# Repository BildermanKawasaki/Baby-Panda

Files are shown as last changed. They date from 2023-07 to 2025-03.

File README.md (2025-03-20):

# Baby-Panda 🐼
#### CoreXY Continuous Printing

Baby Panda is a CoreXY printer with conveyor build plate to enable affordable high quality continuous printing. The motion system is based on the [Voron 2.4](https://vorondesign.com/voron2.4), with z motor mounts and skirts modified to accommodate the conveyor.  The design is intended to repurpose as many parts as possible from a pair of Ender 3s.

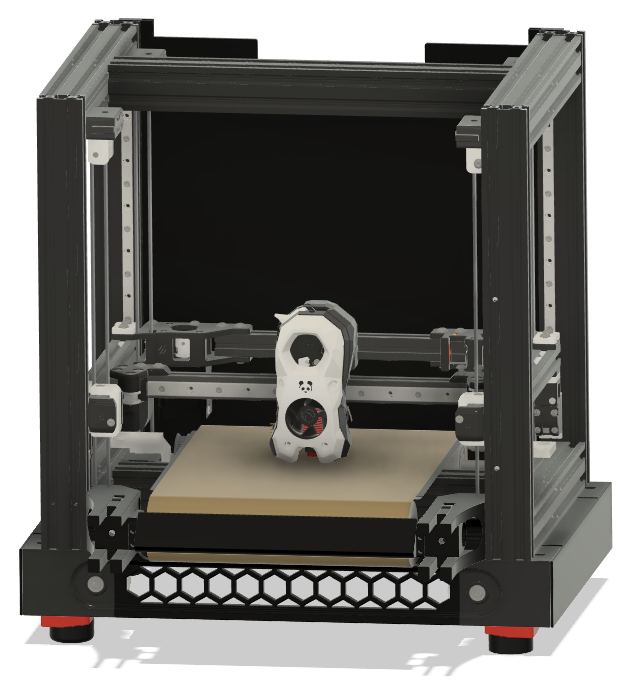
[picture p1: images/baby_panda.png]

If you like this project, please consider <a href="https://www.ko-fi.com/robxberty">tipping</a>!
## Building Baby Panda
There are currently no build instructions specific to Baby Panda, so but the [Voron 2.4r2 assembly manual](https://github.com/VoronDesign/Voron-2/raw/Voron2.4/Manual/Assembly_Manual_2.4r2.pdf) can be used for the most part, along with the following reasources for the Baby Panda-specific parts:
* [BOM](https://github.com/robwaldhauser/Baby-Panda/blob/main/BOM%20Spreadsheet.ods) - Baby Panda bill of materials (.ods format)
* [STLs](https://github.com/robwaldhauser/Baby-Panda/tree/main/STLs) - model files for each part
* [CAD](https://github.com/robwaldhauser/Baby-Panda/tree/main/CAD) - An archive containing a .step file with a fully assembled Baby Panda

If you have any questions, or want to see pictures and videos of builds, check out the #🐼baby-panda channel in the [Build Biome Discord server](https://discord.gg/SpCVg9wG). 

## Ender 3 Parts Reuse
As mentioned above, one of the goals of this project is to repurpose parts from Ender 3s that are sitting around gathering dust. Some of the parts that can be reused include:
* All base 4040 extrusions (Pro/V2)
* Y 4040 extrusion (Pro\*)
* 4020 extrusions (Pro/V2)
* Power supply
* Mainboards\**
* Motors
* Bed carriage
* Heated bed
* Some wiring

\*V2 Y 4040 extrusion could be reused with spacers
\*\*A total of 8 motors drivers are needed, but if you have 2 mainboards they can both be used

## The Belt Assembly
This assembly is the heart of the project. It adds one additional stepper motor to the BOM. There is nothing official released yet, but several people in the Discord are working on macros to make it work. The purpose of the belt is to eject printed parts automatically after printing so that another job can run immediately and without intervention. It is not intended to move during a print as X-Y movement is handled by the coreXY motion system.
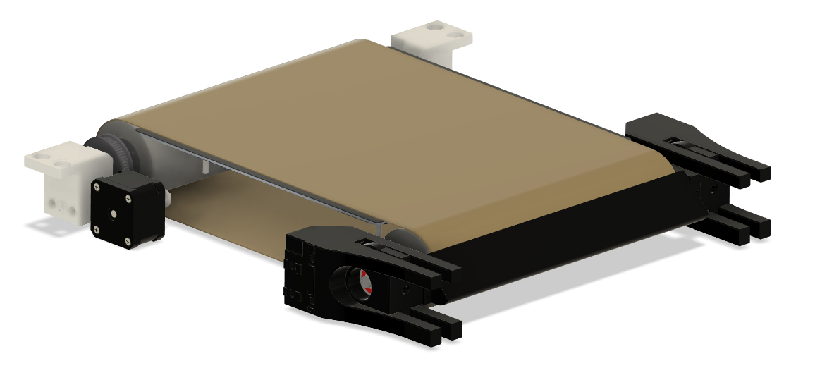
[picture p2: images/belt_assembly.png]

<p><em>Belt assembly</em></p>

## The Frame
The standard Baby Panda frame can be built entirely from extrusions salvaged from 2 Ender 3s. Ender 3 pro is ideal. 3V2 can work, but the Y extrusion is slightly shorter. This can be worked around using spacers or by buying a longer extrusion.

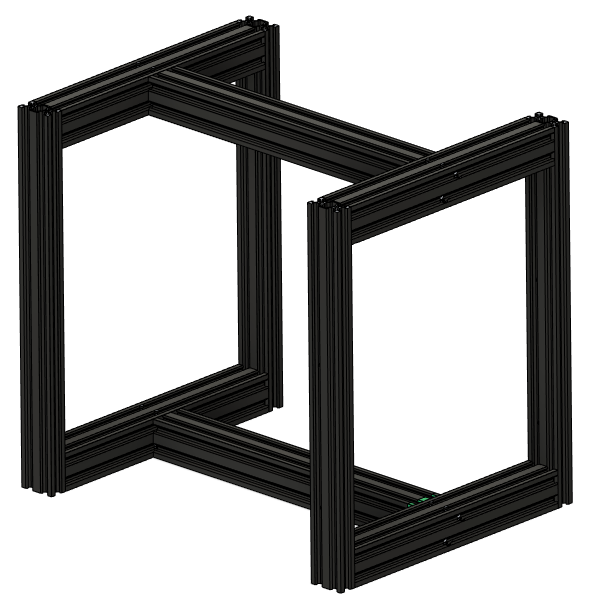
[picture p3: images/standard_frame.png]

<p><em>Standard frame</em></p>

<p>In the standard configuration, the 3 4040 extrusions from the base of one Ender form the base of the Baby Panda frame, and the base extrusions of the other Ender  form the top. The uprights from each ender, which will need to be drilled out for blind joints using the <a href="https://github.com/robwaldhauser/Baby-Panda/blob/main/STLs/Drilling%20Jig.stl">jig</a> available in the CAD section, connect the top of the frame to the bottom in each corner. In case you're not familiar with drilling/tapping new blind joints, <a href="https://www.youtube.com/watch?v=2dvbn0rWA60&ab_channel=CanuckCreator">this video</a> is really helpful. Optionally, 2 additional 2020 extrusions can be installed for extra rigidity and to help enclose the printer.</p>

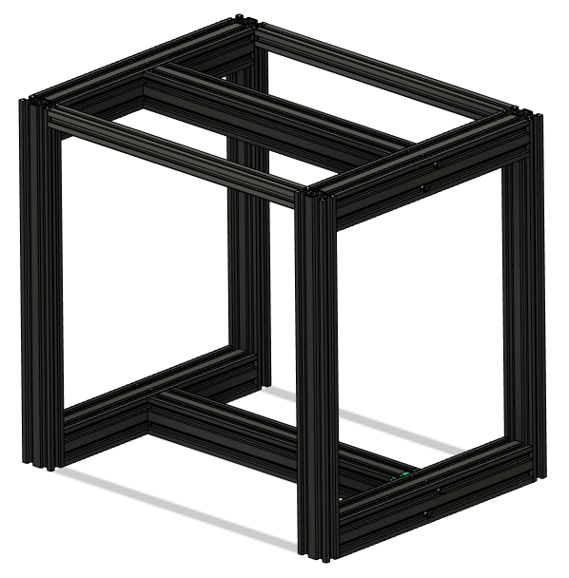
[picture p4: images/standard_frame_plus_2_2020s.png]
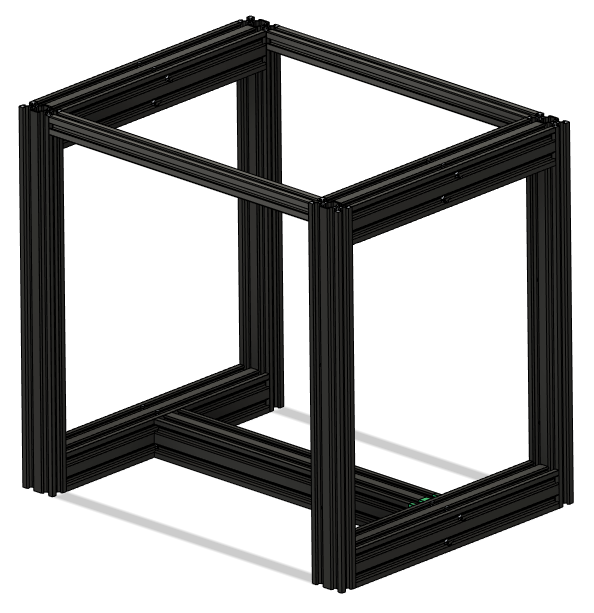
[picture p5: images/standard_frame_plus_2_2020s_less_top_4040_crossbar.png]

<p><em>A couple options for placement of additional 2020 extrusions</em></p>

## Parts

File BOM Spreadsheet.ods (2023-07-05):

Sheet: BOM
Required | Category | Item | URL | Qty | Subtotal | Total
Y | Motion | Linear Rail for X Axis - MGN12H, 280mm | https://www.aliexpress.com/item/3256804722090559.html | 1 | $11.93 | $11.93
Y | Motion | Linear Rail for Y Axis - MGN9H, 220mm | https://www.aliexpress.com/item/3256804722090559.html | 2 | $9.18 | $18.36
Y | Motion | Linear Rail for Z Axis - MGN9H, 300mm | https://www.aliexpress.com/item/3256804722090559.html | 4 | $10.45 | $41.80
Y | Motion | Voron Motion Kit | https://www.aliexpress.com/item/3256803752663278.html | 1 | $53.39 | $53.39
 | Hotend Assembly | Stealthburner Parts | https://www.aliexpress.us/item/3256804449233315.html | 1 | $41.85 | $41.85
 | Hotend Assembly | Tap | https://www.aliexpress.com/item/3256805352633425.html | 1 | $20.80 | $20.80
 | Motherboard | M8P+CB1+8TMC2209 | https://biqu.equipment/products/manta-m4p-m8p?variant=39847239155810 | 1 | $98.68 | $98.68
 | Hotend Assembly | SB2209 CAN for Stealthburner | https://biqu.equipment/products/bigtreetech-ebb-sb2209-can-v1-0?variant=40214282731618 | 1 | $25.68 | $25.68

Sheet: Sheet1
 | Part | Path | Github Repo | Qty | Function Part
Z Axis | NEW_z_drive_main_a_x2
 | NEW_z_drive_main_b_x2
 | z_drive_retainer_a_x2.stl | STLs/Z_Drive | VoronDesign/Voron-2 | 2 | TRUE
 | z_drive_retainer_b_x2.stl | STLs/Z_Drive | VoronDesign/Voron-2 | 2 | TRUE
 | [a]_belt_tensioner_a_x2.stl | STLs/Z_Drive | VoronDesign/Voron-2 | 2 | TRUE
 | [a]_belt_tensioner_b_x2.stl | STLs/Z_Drive | VoronDesign/Voron-2 | 2 | TRUE
 | [a]_z_drive_baseplate_a_x2.stl | STLs/Z_Drive | VoronDesign/Voron-2 | 2 | TRUE
 | [a]_z_drive_baseplate_b_x2.stl | STLs/Z_Drive | VoronDesign/Voron-2 | 2 | TRUE
 | z_tensioner_bracket_a_x2.stl | STLs/Z_Idlers | VoronDesign/Voron-2 | 2 | TRUE
 | z_tensioner_bracket_b_x2.stl | STLs/Z_Idlers | VoronDesign/Voron-2 | 2 | TRUE
 | [a]_z_tensioner9mm.stl | STLs/Z_Idlers | VoronDesign/Voron-2 | 4 | TRUE

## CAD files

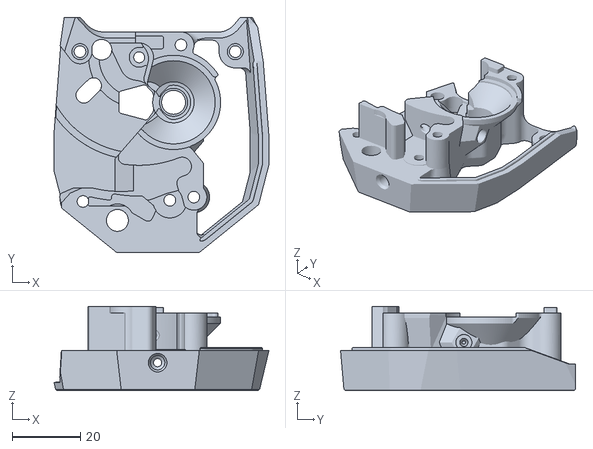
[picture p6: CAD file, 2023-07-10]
STLs/Voron-Stealthburner-main/Clockwork2/main_body.stl
62.8 x 68.7 x 24.7

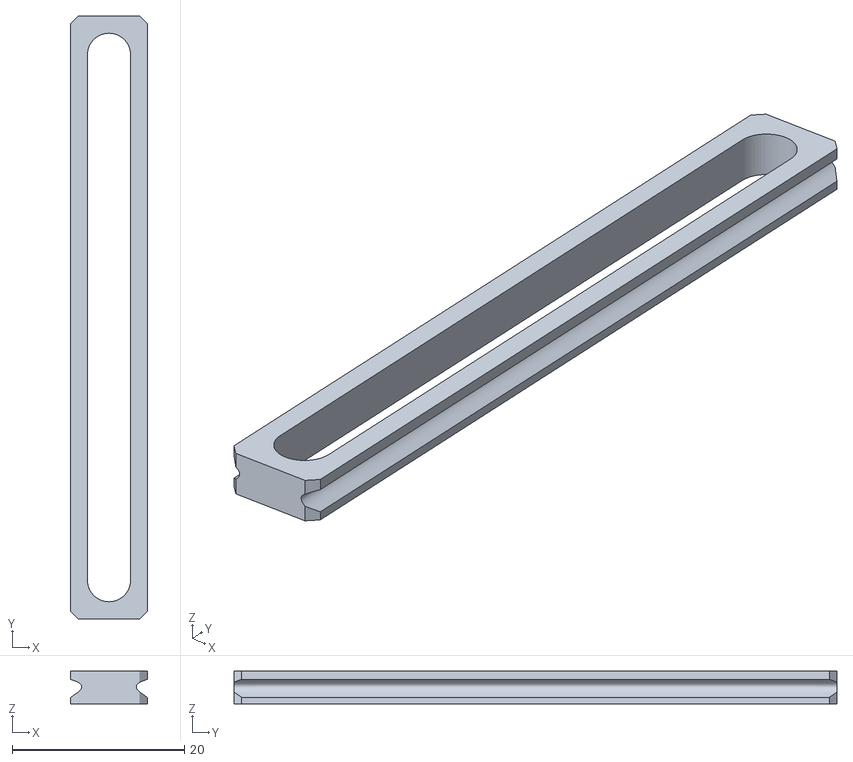
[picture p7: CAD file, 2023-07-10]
STLs/Voron-Tap-main/MGN9_Assembly_Tool.stl
8.90 x 70.0 x 3.80

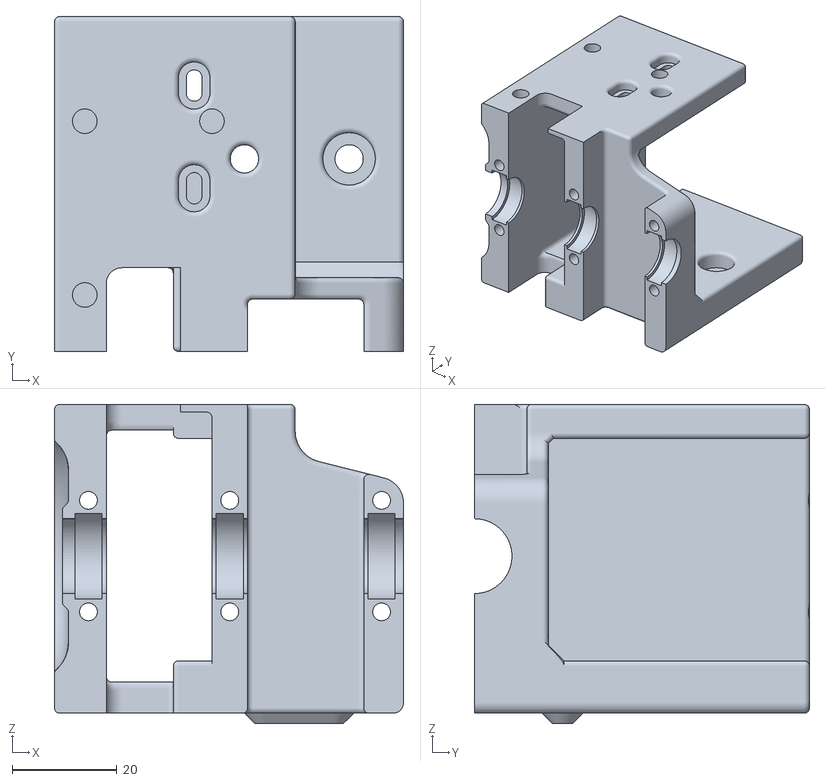
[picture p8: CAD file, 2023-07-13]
STLs/Z_Drive/BP_z_drive_main_b_x2_wSupport.stl
66.7 x 64.0 x 61.0

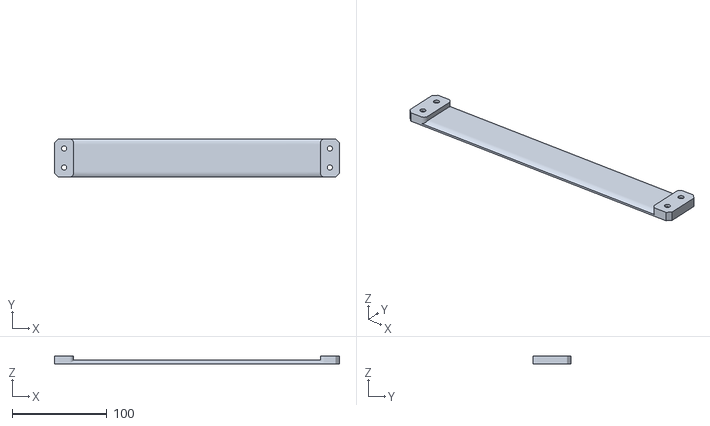
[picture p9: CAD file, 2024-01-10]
STLs/Baby Panda Parts/Belt Shield.stl
300.1 x 40.0 x 8.74

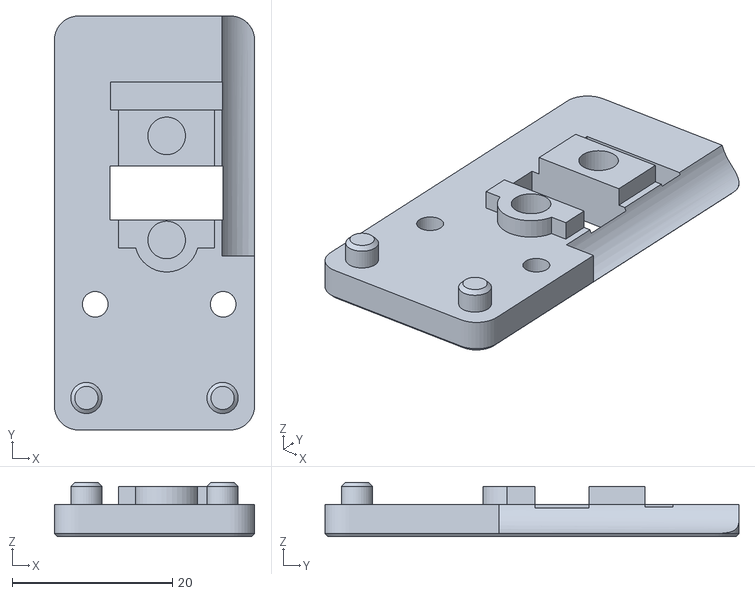
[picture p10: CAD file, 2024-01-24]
STLs/CAN/Y_endstop_[a]_B.STL
25.0 x 51.7 x 6.80

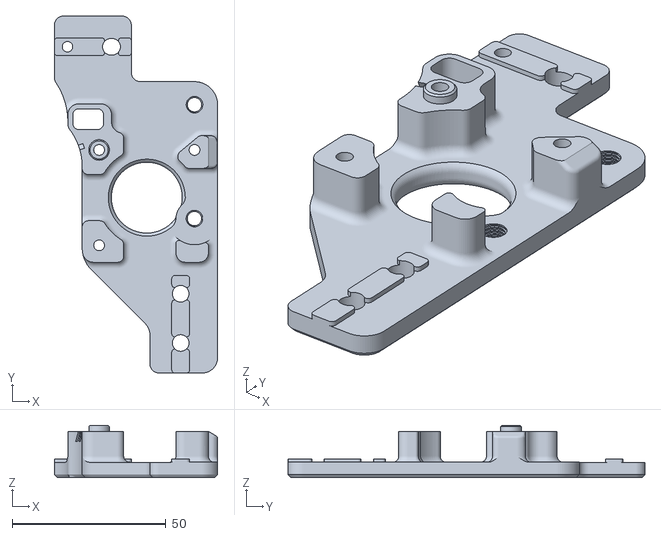
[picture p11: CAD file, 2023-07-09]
STLs/Gantry/AB_Drive_Units/b_drive_frame_lower.stl
53.0 x 116.0 x 17.0

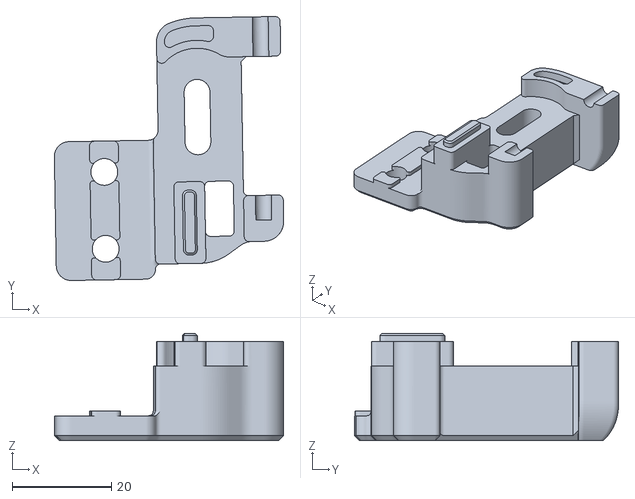
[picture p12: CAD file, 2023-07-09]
STLs/Gantry/Front_Idlers/front_idler_left_upper.stl
46.2 x 53.2 x 21.6

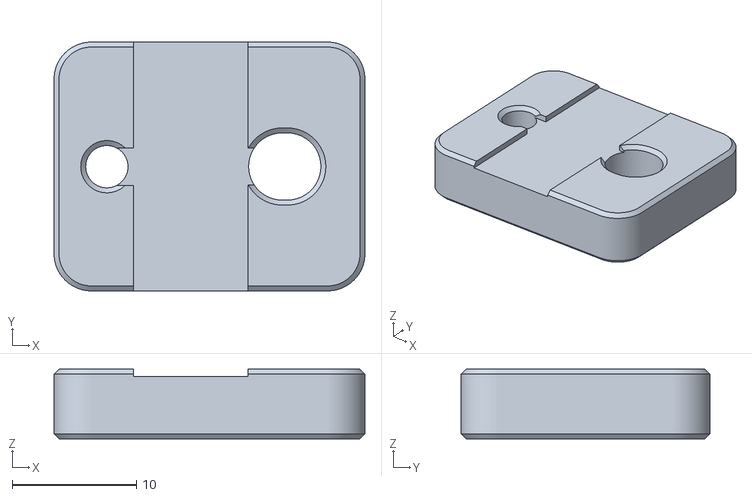
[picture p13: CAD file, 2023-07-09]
STLs/Gantry/ignore - [a]_z_belt_clip_lower_x4.stl
25.0 x 20.0 x 5.60

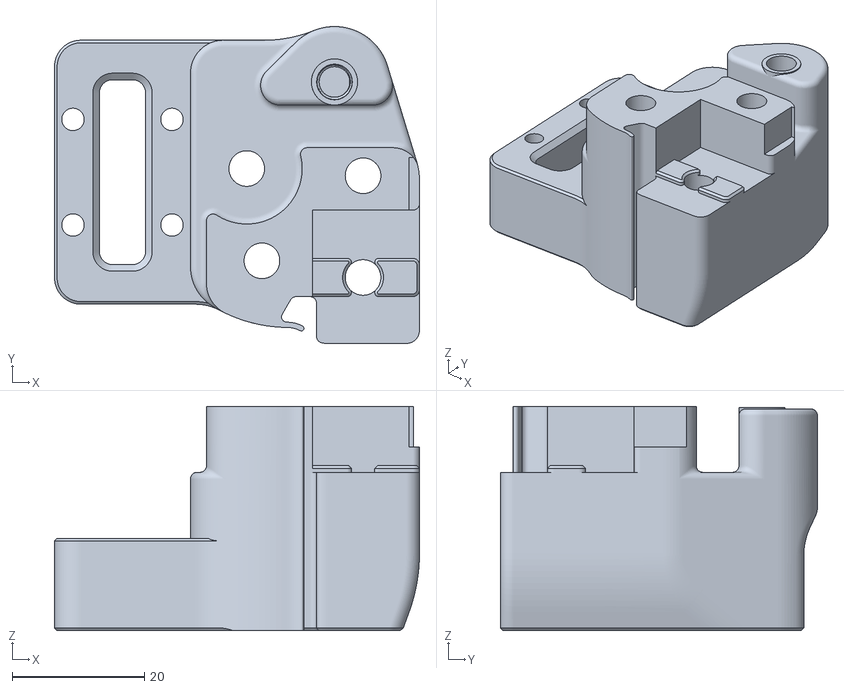
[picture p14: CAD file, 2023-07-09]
STLs/Gantry/X_Axis/XY_Joints/xy_joint_right_lower_MGN12.stl
55.3 x 48.0 x 34.0

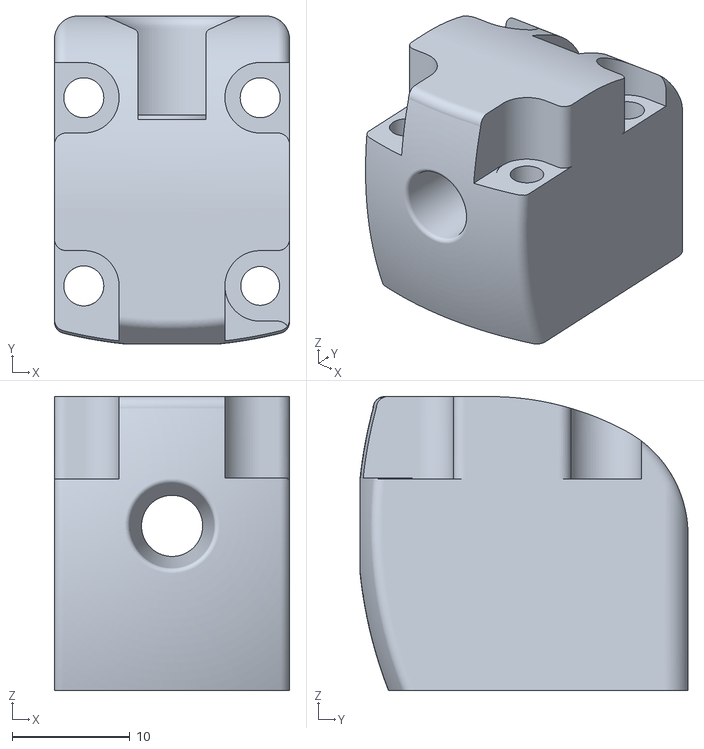
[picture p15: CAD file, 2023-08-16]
STLs/Gantry/Z_Joints/BP_z_joint_lower_x4.stl
20.0 x 27.9 x 25.0

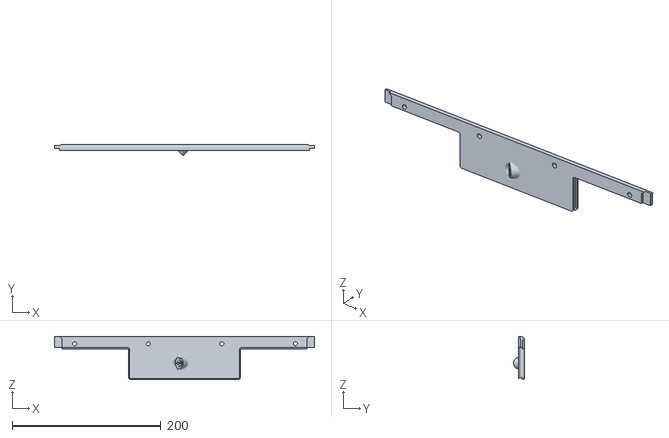
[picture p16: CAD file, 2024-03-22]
STLs/Panels/Back Panels/PTFE Passthrough.stl
350.0 x 14.6 x 58.2

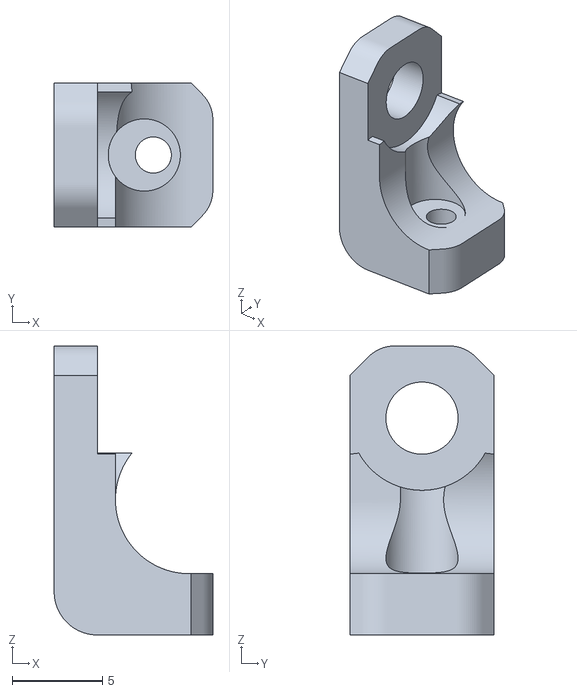
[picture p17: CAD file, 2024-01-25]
STLs/Panels/Bottom Panels/PSU Clip.stl
8.80 x 8.00 x 16.0

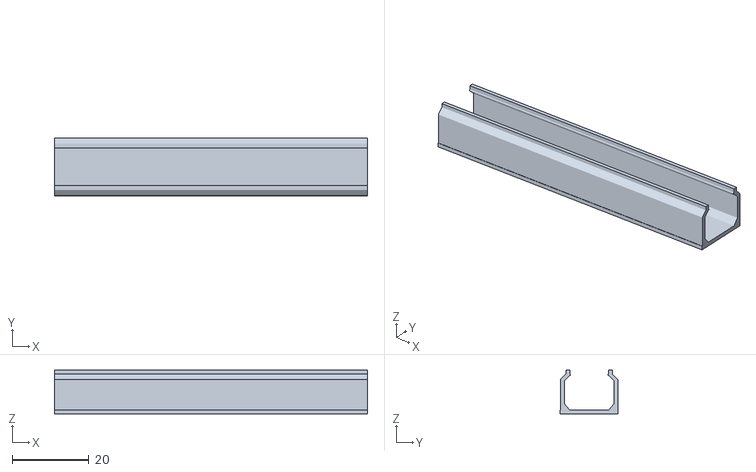
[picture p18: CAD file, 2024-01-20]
STLs/Panels/Cable Track.stl
81.6 x 15.0 x 11.5

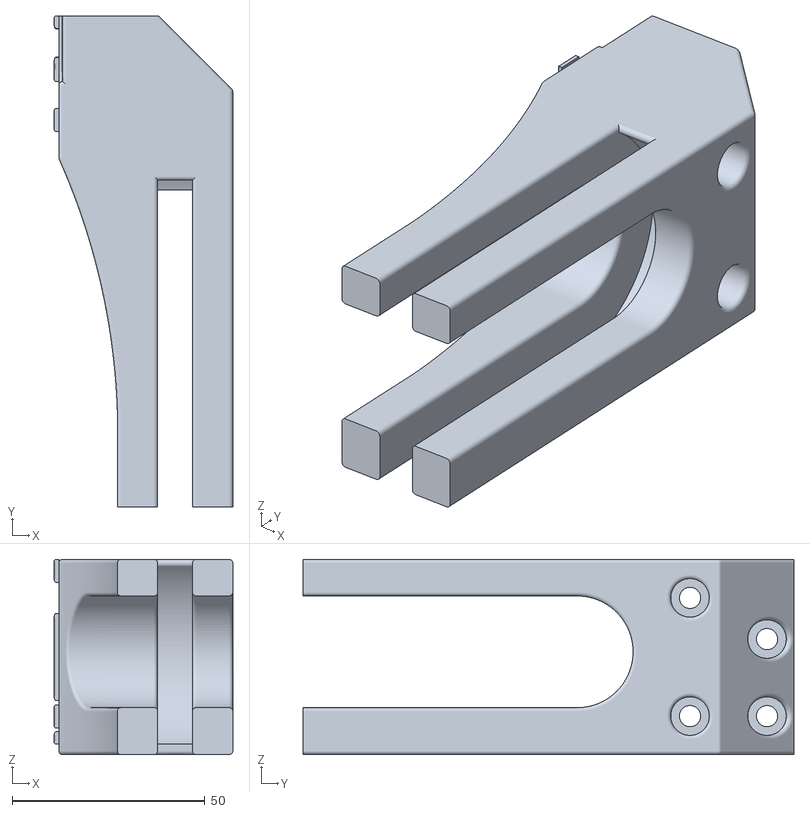
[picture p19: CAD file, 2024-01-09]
STLs/Roller Parts/Left Roller Arm_x2_but_mirrored.stl
46.4 x 127.5 x 50.7

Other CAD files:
STLs/Z_Drive/BP_z_drive_main_a_x2_wSupport.stl
STLs/Skirt/Front Skirt.stl
STLs/sturdy_handles.stl
STLs/Voron-Stealthburner-main/Clockwork2/cable_door.stl
STLs/3mm riser (opt).stl
STLs/59mm Roller.stl
STLs/BP_Roller_Blade.stl
STLs/Baby Panda Spool Holder.stl
STLs/CAN/Drag Chain Lower Mount.stl
STLs/CAN/Extrusion Cover.stl
STLs/CAN/TPU Umbilical Holder.stl
STLs/CAN/Y_endstop_A.STL
STLs/Drilling Jig.stl
STLs/Gantry/AB_Drive_Units/[a]_z_chain_retainer_bracket_x2.stl
STLs/Gantry/AB_Drive_Units/a_drive_frame_lower.stl
STLs/Gantry/AB_Drive_Units/a_drive_frame_upper.stl
STLs/Gantry/AB_Drive_Units/b_drive_frame_upper.stl
STLs/Gantry/Front_Idlers/[a]_tensioner_left.stl
STLs/Gantry/Front_Idlers/[a]_tensioner_right.stl
STLs/Gantry/Front_Idlers/front_idler_left_lower.stl
STLs/Gantry/Front_Idlers/front_idler_right_lower.stl
STLs/Gantry/Front_Idlers/front_idler_right_upper.stl
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

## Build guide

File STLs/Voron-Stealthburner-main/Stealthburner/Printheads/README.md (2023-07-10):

# Printheads for Stealthburner.

Choose files containing ***front*** based on your hotend and ***rear_cw1*** / ***rear_cw2*** based on whether you're using the original Clockwork (CW1) or the new Clockwork2 (CW2) extruder.

## Printhead Compatibility:

| Hotend | Compatible Parts | Notes |
|---|---|---|
| Phaetus/Trianglelab Dragon | (P-DRG) | Remove the screws attaching the groove-mount adaptor to access the hard mounting points. |
| Phaetus BMO | (P-BMO) | Unscrew the groove-mount adaptor to access the hard mounting points. |
| Phaetus BMS (6 fins) | (P-BMS6) | Phaetus has two versions of the BMS; Count the number of fins on your hotend to determine your version. |
| Phaetus BMS (7 fins) | (P-BMS7) | Phaetus has two versions of the BMS; Count the number of fins on your hotend to determine your version. |
| Phaetus Rapido | (P-RPD) | Only the standard Rapido is supported (No UHF support). See the additional note about [heatsink orientations](phaetus_rapido/README.md). |
| E3D Revo Micro | (E-RM) | If your mount nut has a ridge on it, put that to the top. |
| E3D Revo Six | (E-V/R6) |  |
| E3D V6 | (E-V/R6) |  |
| E3D Revo Voron | (E-RV) |  |

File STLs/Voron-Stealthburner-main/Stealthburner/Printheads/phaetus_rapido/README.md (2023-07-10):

## Phaetus Rapido High Flow mount

### BOM

- One front printed part
- One rear printed part
- Heatset inserts
- Four M2.5x8 socket screws, which should be provided in your Rapido kit
- Two M3x12 socket screws
- PTFE tube

### Instructions

- Add two heatset inserts on the front printed part. Add an additional two if you plan to use the ADXL PCB mount.
- Remove the adapter and bowden collet from the Rapido's heatsink by unscrewing the two M2.5x5 screws:
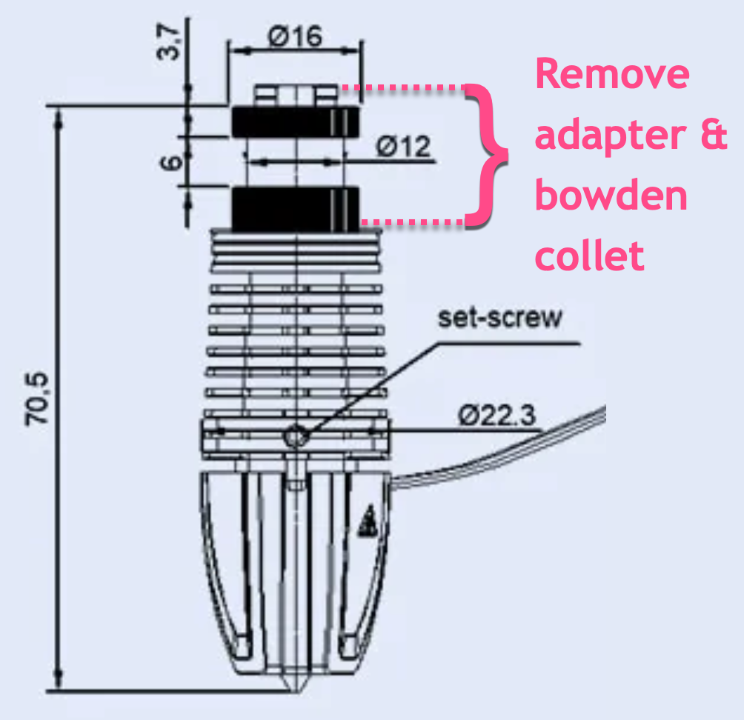
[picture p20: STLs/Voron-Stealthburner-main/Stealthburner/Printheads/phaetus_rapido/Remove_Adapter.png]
Remove adapter
  
- Place the hotend in the front printed part and secure it by screwing two M2.5x8 screws into the heatsink.
- Secure the front and rear printed parts together with two M3x12 screws.
- Secure the hotend with the rear part by screwing two M2.5x8 screws into the heatsink.
- Insert the PFTE tube at the top of the mount.

### A note about Rapido orientations

Depending on where the Rapido is sourced, it may come in one of two unsupported heatsink orientations.

To change the orientation of heatsink, first loosen the grub screw on the side and then remove the 3 screws around the heater core. The heatsink can then be rotated +/- 120° into the correct orientation. Be careful not to over-tighten the screws when reassembling as this could cause the heatbreak to bend.

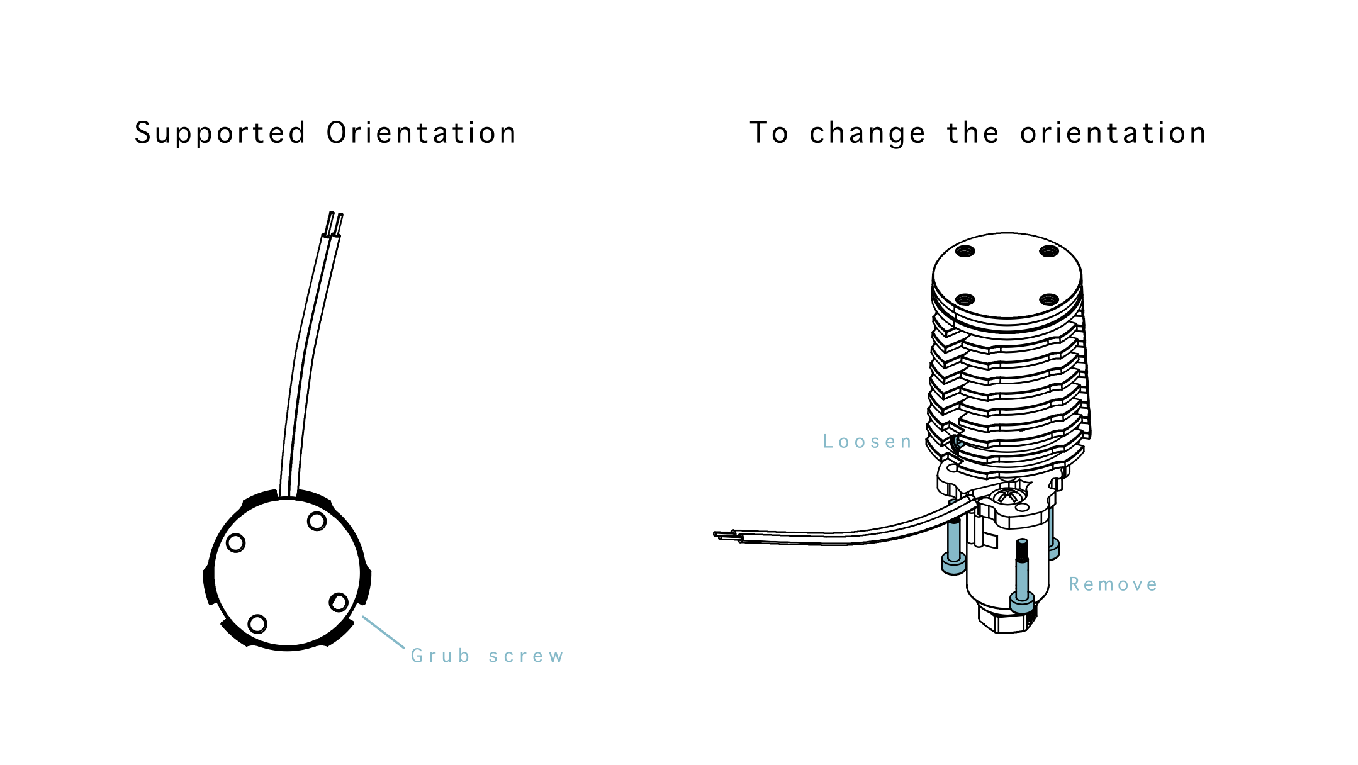
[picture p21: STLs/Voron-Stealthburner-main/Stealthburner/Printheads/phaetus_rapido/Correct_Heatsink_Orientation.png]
Correct Heatsink Orientation


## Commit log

2023-06-30 Spreadsheet for tracking BOM and Printed Parts
    [BOM Spreadsheet.ods]
2023-07-05 Update BOM Spreadsheet.ods
    [BOM Spreadsheet.ods]
2023-07-09 Added stl files to git
    [DRAFT_z_drive_main_a_x2.stl, [a]_tensioner_left.stl, [a]_tensioner_right.stl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]
2023-07-13 Add BP Specific Files
    [BP_z_drive_main_a_x2.stl, BP_z_drive_main_b_x2.stl, BP_z_motor_mount_a_x2.stl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]
2023-07-17 adding rubber feet
    [BP_rubber_foot_x4_[print_in_tpu].stl]
2023-07-17 updated feet
    [BP_rubber_foot_x4_[print_in_tpu].stl]
2023-07-18 Create Drilling Jig.stl
    [Drilling Jig.stl]
2023-08-14 Added PandaBurner
    [Panda_Diffuser.stl, Panda_Diffuser_Mask.stl]
2023-08-16 short z joints added
    [Corner Cube.stl, DRAFT_z_drive_main_a_x2.stl, bp_bed_spacer_x4.stl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]
2023-08-16 updated bed spacer
    [[a]_bp_z_joint_belt_clamp_lower_x4.stl, bp_bed_spacer_x4.stl]
2023-08-17 naming updates
    [DRAFT_z_drive_main_a_x2.stl]
2023-09-26 Create Rear Roller Mount.stl
    [Rear Roller Mount.stl]
2023-09-26 Create 59mm Roller.stl
    [59mm Roller.stl]
2023-11-09 roller updates
    [Left Roller Arm_x2_but_mirrored.stl, Rear Roller Mount_x2_but_mirrored.stl, Tensioner Arm Cap_x2.stl]
2023-11-09 Create 57mm Roller_x2.stl
    [57mm Roller_x2.stl]
2023-11-14 Create Front Bearing Holder_x2_but_mirrored.stl
    [Front Bearing Holder_x2_but_mirrored.stl]
2023-11-15 Update Front Bearing Holder_x2_but_mirrored.stl
    [Front Bearing Holder_x2_but_mirrored.stl]
2023-11-17 Create Front Skirt.stl
    [Front Skirt.stl]
2023-12-05 updated blade and bearing holders
    [BP_Roller_Blade.stl, Front Bearing Holder_x2_but_mirrored.stl, Left Roller Arm_x2_but_mirrored.stl]
2024-01-09 Update Left Roller Arm_x2_but_mirrored.stl
    [Left Roller Arm_x2_but_mirrored.stl]
2024-01-10 Create Belt Shield.stl
    [Belt Shield.stl]
2024-01-18 Adding Skirts and Panels
    [Fan Cover.stl, Front Skirt.stl, Left Skirt.stl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]
2024-01-18 Update Rear Skirt.stl
    [Rear Skirt.stl]
2024-01-18 Fixed Skirts, Added Din
    [Din Rail.stl, Front Skirt.stl, Rear Skirt.stl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]
2024-01-18 Update Right Skirt.stl
    [Right Skirt.stl]
2024-01-18 Slotted holes for easier install
    [Panel A.stl, Panel B.stl, Panel C.stl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]
2024-01-18 fixed lower panels
    [Panel A.stl, Panel B.stl, Panel C.stl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]
2024-01-25 Create PSU Clip.stl
    [PSU Clip.stl]
2024-01-29 removed old stls
    [Back Panel Rail Bottom Right.stl, Back Panel Rail Right.stl, Back Panel Rail Top Right.stl]
2024-01-29 update back panels
    [6x Back Panel (62mm).stl]
2024-01-29 fixed count
    [5x Back Panel (62mm).stl]
2024-03-22 Create PTFE Passthrough.stl
    [PTFE Passthrough.stl]
2024-03-22 Fixed Z drive retainer
    [z_drive_retainer_a_x2 (need to be replaced).stl, z_drive_retainer_a_x2.stl, z_drive_retainer_b_x2 (need to be replaced).stl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]
2024-03-25 update z joints
    [BP_z_joint_lower_x4.stl, BP_z_joint_upper_x4.stl, ignore - [a]_z_belt_clip_lower_x4.stl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]
2025-03-06 Updated Readme with additional information
    Added a more detailed description of the project. Included links to BOM/STLs/CAD/Discord. Added description of the frame including some visual aids.
2025-03-07 Update README.md
    added link to voron 2.4r2 assembly manual
2025-03-07 README.md updates
    Removed whitespace from images
    Added image of belt assembly
    Added information about ender part reuse and about the belt assembly
2025-03-07 Updated README.md
    Added CAD screenshot of BP to introduction
2025-03-08 Updated README.md
    Added link to blind joint instructional vid
